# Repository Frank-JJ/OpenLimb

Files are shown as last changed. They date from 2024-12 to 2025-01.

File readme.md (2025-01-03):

# OpenLimb

This project contains code for the OpenLimb project at University of Southern Denmark, SDU, for the Fall 2024 semester.

This project consists of the design and construction of a bio-inspired robot, with limbs made of soft material, allowing for locomotion.

The code in this repository enables the functionality of the robot, when it is assembled correctly.

## Building the robot

### Components List

- **1 pcs.**   Raspberry Pi Pico W
- **1 pcs.** Android-compatible Bluetooth gamepad, e.g. 8BitDo Pro 2 Bluetooth Gamepad
- **4 pcs.**   MG90S Micro Servo Motor
- **1 pcs.**   Li-ion-PO 7.4V 1000mAh battery
- **1 m.**      Fishing line
- **4 pcs.**   5V Linear Voltage Regulator (L7805ACV)
- **10 pcs.**  Female-Female Jumper Cables
- **1 pcs.**   USB to Micro-USB cable
- **12 pcs.** M2×7mm bolts
- **4 pcs.**  M2×16mm bolts
- **16 pcs.** M2 nuts
- **16 pcs.** M2 washers

In addition to the components listed, it is highly recommended to acquire a fireproof battery bag, a balanced cell charger, and a over-, under-charge alarm for the battery. Handle the Li-ion battery with care!
The electrical circuit may require more or less jumper cables, and with different connectors.

### Manufacturing and 3D printing

Any modern 3D printer should be able to print the parts required for this project. You will need either PLA or PETG for:

- Base
- Battery Mount
- Feet
- Mounting clip
- Pulley
- Servo mount

Besides that, the legs need to be printed in PETG to be flexible and the fins need to be printed in TPU for bendability and grippyness.

### Assembly of Robot

Now that all the parts has been manufactured, it is time to assemble the robot. The robot can be assembled in different configurations to meet a specific task at hand. This configuration can be changed later if necessary.

#### Assembly of Limbs

One limb is constructed using the following parts:

- **1 pcs.**   Flexible 3D-printed or laser cut sheet
- **1 pcs.**   3D-printed magnet/motor mount
- **1 pcs.**   MG90S Micro Servo motor
- **1 pcs.**   Friction pad
- **2 pcs.**   Neodymium Magnets
- **1 pcs.**   3D-printed foot
- **$\approx 30cm$**   Fishing line
- **1 pcs.**   Pulley

Assemble the limb by following these steps:

- STEPS

#### Connecting Limbs to the Body

The limbs can be attached in many configurations around the robot's body. Determine a suitable position for the limb, and then dis-attach the ring cover from the underside of the robot's body with a twisting motion counter-clockwise. Carefully place two Neodymium Magnets in the indents at the chosen position in the robot body. Secure the ring cover over the magnets, by twisting it clockwise until it's locked in place.

Turn the robot around, and place the 3D-printed magnet/motor mount at the end of the limb above the magnets in the body. When the limb has snapped in place, insert a pin into the hole in the magnet/motor mount to lock it in place.

Repeat for the amount of limbs in the desired configuration.

#### Electrical Assembly

- **1 pcs.**   Raspberry Pi Pico W
- **1 pcs.**   Li-ion-PO 7.4V 1000mAh battery
- **4 pcs.**   5V Linear Voltage Regulator (L7805ACV)
- **10 pcs.**  M Jumper Cables
- **4 pcs.**   M3x15 Machine Screws

Secure the Raspberry Pi Pico W with four M3x15 machine screws in the middle of the robot body. Solder or use quick connect screw terminal blocks to replicate the schematic in [Electrical Schematic](#electrical-diagram):

#### Electrical Diagram

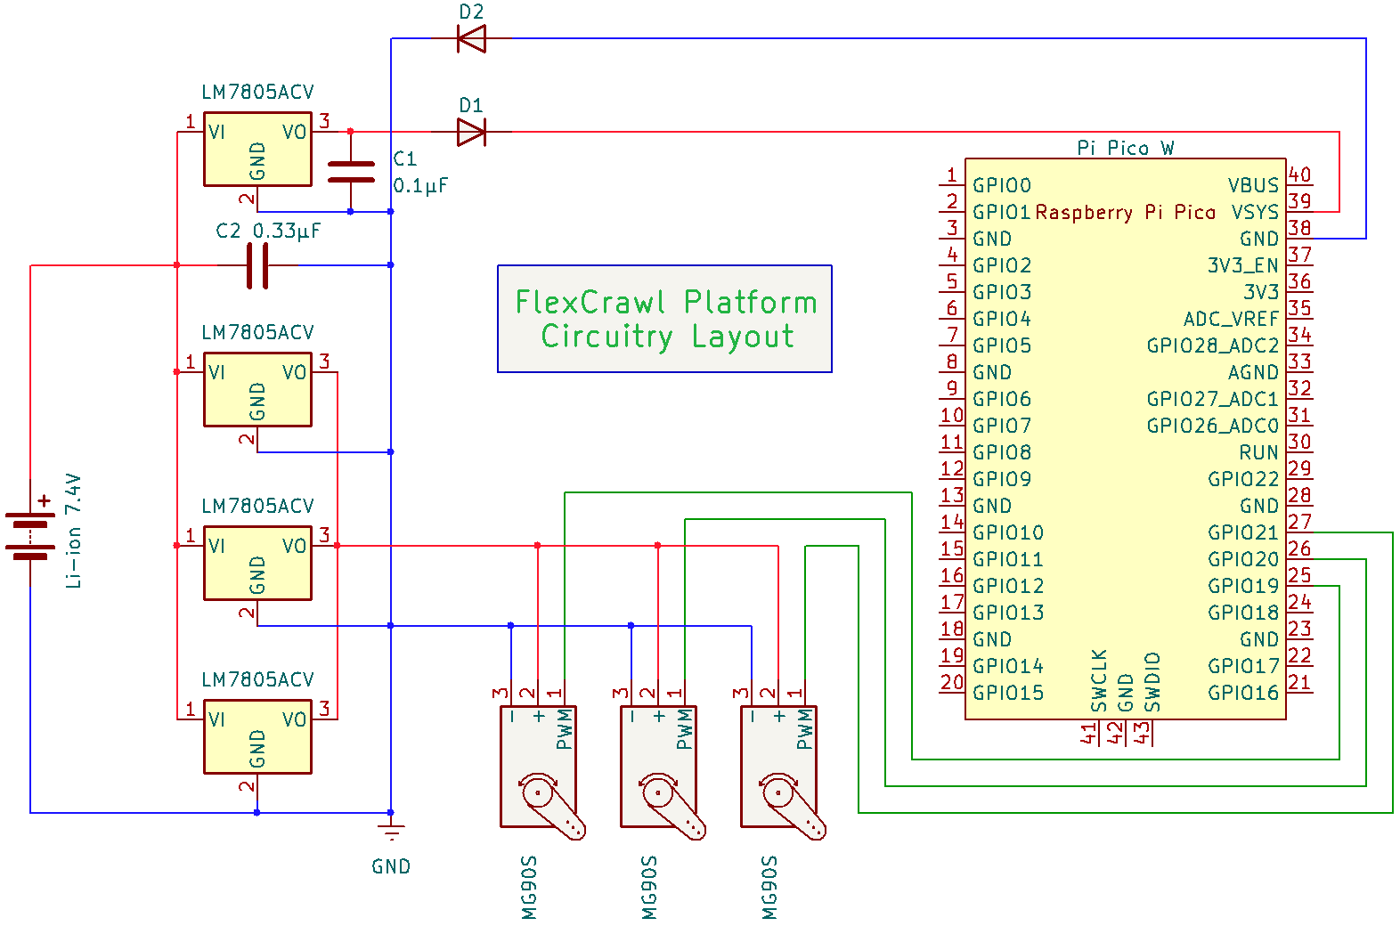
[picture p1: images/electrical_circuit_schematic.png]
Schematic showing the different components and their connections


Use electrical tape to fasten components to the body if necessary, but keep in mind to keep weight as low as possible.

## Using the code

The "flexControl" arduino project contains code that should be run on the Raspberry Pi Pico W to control the servos, according to user defined gaits.

The code consists of three parts:

- A bluetooth handler, for obtaining user input from a bluetooth compatible joystick.
- The gait machine, which linearly interpolates between defined motor commands, to run a gait.
- The motor controller, which outputs the interpolated values from the gait machine to the servos on the limbs.

### Configuring the three motors and limbs

The limb and motor configuration, when limited to three each, can be updated simply in [flexControl/gaitMachine.cpp](flexControl/gaitMachine.cpp):

Set the motor configurations in the MotorConfigVector variable. A limb can be placed on either the left, center, or right side of the body.
A servo can be placed on either the left or right side of the servo mount as seen from the body out along the length of the limb.

```cpp
line 180:   MotorConfigVector motorConfigVector = {
line 181:     {BodySide::Left, ServoSide::Left},
line 182:     {BodySide::Center, ServoSide::Left},
line 183:     {BodySide::Right, ServoSide::Left}
line 184:   };
```

The index defines the limb and motor. These indexes are further defined in [flexControl/gaitMachine.h](flexControl/gaitMachine.h):

Define the motor id's. These define the order of the motors in regards to what limbs they are attached to.

```cpp
line 15:    enum Motors {Right=0, Tail=1, Left=2};
```

### Defining a gait

#### Example gait

A gait can be defined as follows:

```cpp
GaitStruct Caterpillar = {
  .initialMotorPositions = {0,0,0},
  .gait={
    {Tail,  0.68,  0,    0.2},
    {Left,  0.9,  0,    0.5},
    {Right, 0.9,  0,    0.5},
    {Tail,  0.2,  0.5,  0.2},
    {Left,  0,    0.8,  0.05},
    {Right, 0,    0.8,  0.05},
    {Tail,  0,    0.8,  0.2},
  },
  .gait_time=0.5,
  .gait_amp=0.5
};
```

It must then be inserted into the movementGaits variable in [flexControl/gaitMachine.cpp](flexControl/gaitMachine.cpp):

```cpp
line 177:   GaitVector movementGaits = {Crawler, Caterpillar, TailPush, BackJump};
```

It can then be selected by the arrow or X, B, Y, A buttons of the joystick, by selecting the currect button according to its index in the vector.

#### The code structure

A gait is a vector of motor commands, as well as amplitude and duration parameters and initial motor positions.

The GaitStruct type in [flexControl/gaitMachine.h](flexControl/gaitMachine.h) defines the gait:

```cpp
line 30:    struct GaitStruct{
line 31:      std::vector<float> initialMotorPositions = {0,0,0};
line 32:      Gait gait;
line 33:      float gait_time = 2;
line 34:      float gait_amp = 1;
line 35     };
```

The gait_time parameter is the duration of the gait in seconds. The gait_amp parameter is the amplitude of the gait as a percentage of the max motor value, which is given in degrees:

```cpp
line 90:    float MOTOR_MAX_VAL = 180;
```

The gait parameter is a vector of motorCMD:

```cpp
line 26:    typedef std::vector<motorCMD> Gait;
```

A motorCMD consists of a motor id, amount of gait amplitude in percentage, start time and duration as a percentage of gait duration:

```cpp
line 18:    struct motorCMD{
line 19:      Motors motorID;
line 20:      float amount;
line 21:      float start;
line 22:      float duration;
line 23:    };
```

### Changing the number of motors and limbs

The default code allows for three servos, but this can be modified.

#### Within the motor controller

Go into: [flexControl/motorControl.h](flexControl/motorControl.h)

Define the number of servos:

```cpp
line 36:    void loop(std::array<uint8_t, 3> servoVals);
line 39:    static const int NUM_SERVOS = 3;
```

Define the pins for each servo.

```cpp
line 42:    uint8_t servoPins[NUM_SERVOS] = {19,20,21};
```

Pinout for the Raspberry Pi Pico W Follow the pinout for the Raspberry Pi Pico W.

Define the min and max pulse width in microseconds for the min and max angle of each servo (<https://docs.arduino.cc/libraries/servo/>):

```cpp
line 43:    uint16_t servoMins[NUM_SERVOS] = {544,544,544};
line 44:    uint16_t servoMaxs[NUM_SERVOS] = {2400,2400,2400};
```

#### Within the gait machine

##### Within the h file

Go into: [flexControl/gaitMachine.h](flexControl/gaitMachine.h)

Define the motor id's. These define the order of the motors in regards to what limbs they are attached to.

```cpp
line 15:    enum Motors {Right=0, Tail=1, Left=2};
```

Update the output from the loop function. The 3 should be changed to the number of motors:

```cpp
line 74:    std::array<uint8_t, 3> loop(bluetoothHandler::BluetoothOutput btIn);
```

Do the same for each of the arrays used to store motor values:

```cpp
line 83:    std::array<uint8_t, 3> program_end_motorpos = {0,0,0};
line 84:    std::array<float, 3> prev_M_pos = {0,0,0};
line 85:    std::array<float, 3> M_pos = {0,0,0};
line 87:    std::vector<float> MOTOR_INIT = {0,0,0};
line 98:    std::array<uint8_t, 3> motor_pos_array;
```

##### Within the cpp file

Go into: [flexControl/gaitMachine.cpp](flexControl/gaitMachine.cpp)

Set the motor configurations in the MotorConfigVector variable. A limb can be placed on either the left, center, or right side of the body.
A servo can be placed on either the left or right side of the servo mount as seen from the body out along the length of the limb.

```cpp
line 180:   MotorConfigVector motorConfigVector = {
line 181:     {BodySide::Left, ServoSide::Left},
line 182:     {BodySide::Center, ServoSide::Left},
line 183:     {BodySide::Right, ServoSide::Left}
line 184:   };
```

Add another mapping value to store the interpolated motor value:

```cpp
line 203:   static int M1_mapped = 0, M2_mapped = 0, M3_mapped = 0;
```

Expand the temporary motor position variables:

```cpp
line 217:   // Store initial motor values
line 218:   prev_M_pos[0] = MOTOR_INIT[0];
line 219:   prev_M_pos[1] = MOTOR_INIT[1];
line 220:   prev_M_pos[2] = MOTOR_INIT[2];
line 221:   M_pos[0] = MOTOR_INIT[0];
line 222:   M_pos[1] = MOTOR_INIT[1];
line 223:   M_pos[2] = MOTOR_INIT[2];
```

Expand the mapping and outputtin of motor values:

```cpp
line 266:   // Finally map the modified interpolated motor commands to the currect motor max and min values
line 267:   M1_mapped = mapToMotorValue(M_pos[0]);
line 268:   M2_mapped = mapToMotorValue(M_pos[1]);
line 269:   M3_mapped = mapToMotorValue(M_pos[2]);
line 270:   motor_pos_array = {(uint8_t)M1_mapped, (uint8_t)M2_mapped, (uint8_t)M3_mapped};
```

Expand the initial motor positions output (the {0,0,0}) from the selectGait function:

```cpp
line 303:   return {{0,0,0}, movementGaits[0].gait, 0, 0, 0.5, 0};
```

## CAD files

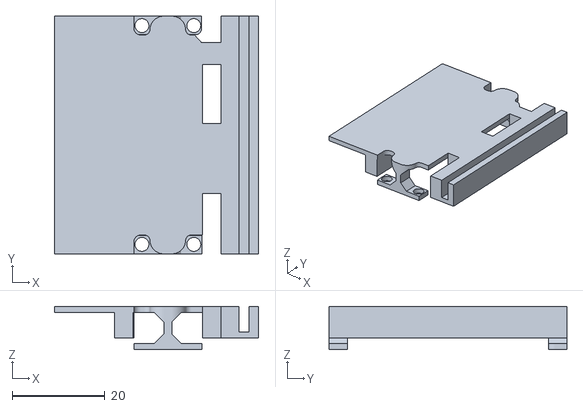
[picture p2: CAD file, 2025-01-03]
3D_Files/BatteryMount.stl
44.1 x 51.4 x 9.40

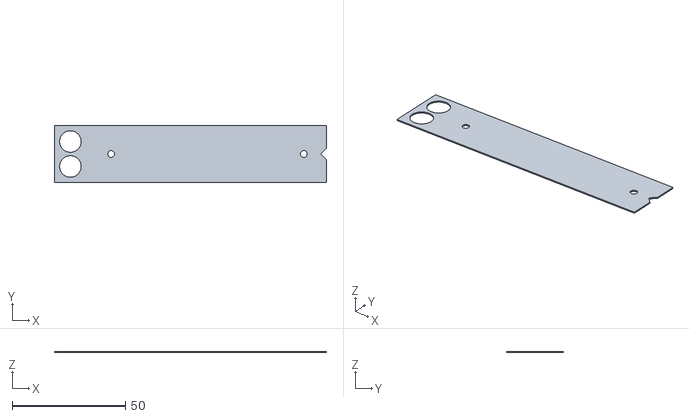
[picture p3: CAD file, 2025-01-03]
3D_Files/Legs/05.stl
120.0 x 25.0 x 0.5

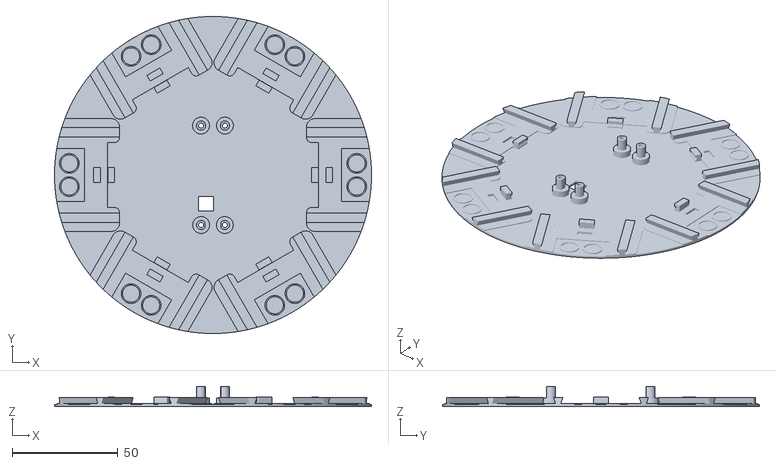
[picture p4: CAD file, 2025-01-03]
3D_Files/Base.stl
150.0 x 150.0 x 9.50

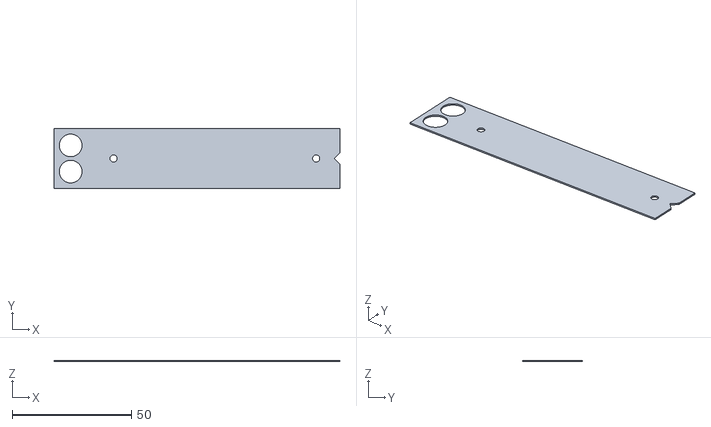
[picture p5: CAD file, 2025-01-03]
3D_Files/Legs/06.stl
120.0 x 25.0 x 0.6

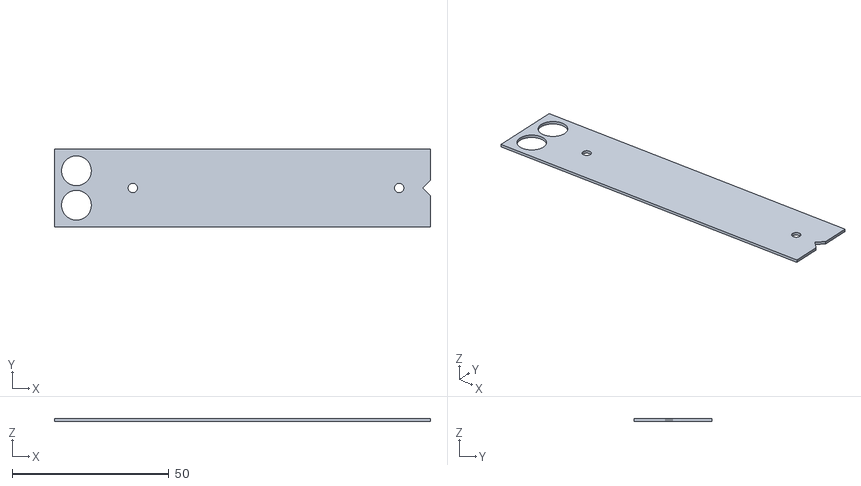
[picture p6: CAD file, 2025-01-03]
3D_Files/Legs/09.stl
120.0 x 25.0 x 0.9

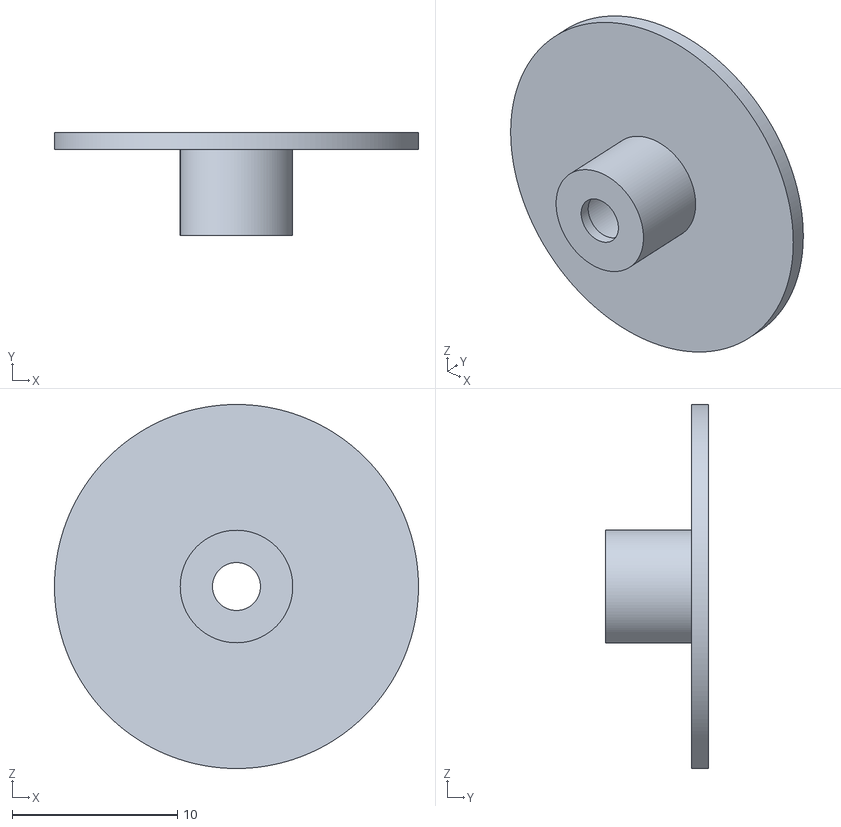
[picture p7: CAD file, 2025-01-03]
3D_Files/Pulley_lid.stl
22.0 x 6.20 x 22.0

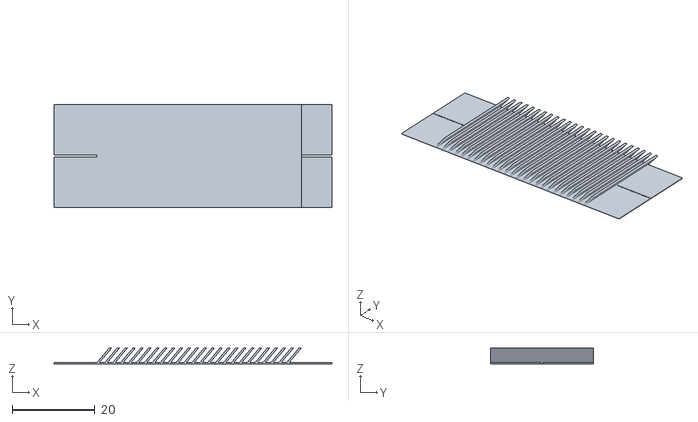
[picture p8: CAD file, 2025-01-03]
3D_Files/Fin.stl
67.4 x 25.0 x 3.82

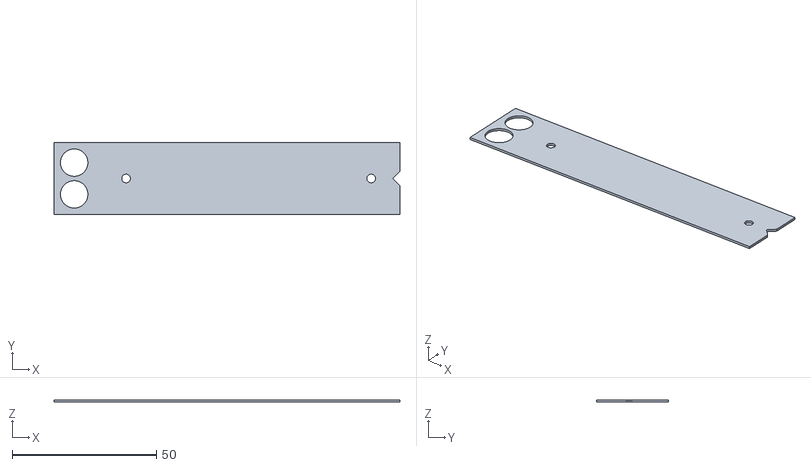
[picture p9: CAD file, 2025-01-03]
3D_Files/Legs/08.stl
120.0 x 25.0 x 0.8

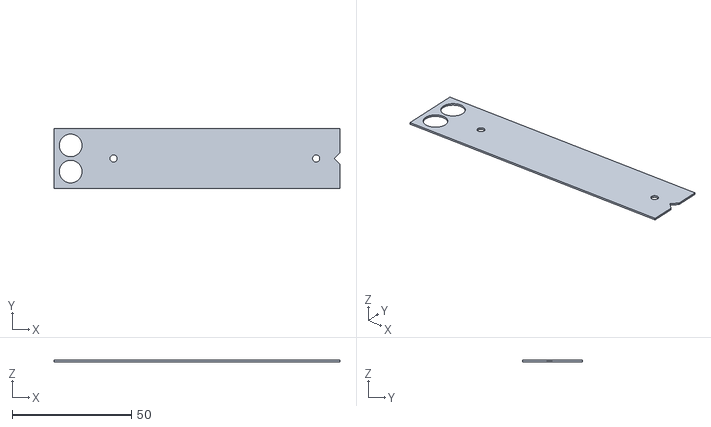
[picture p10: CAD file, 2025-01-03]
3D_Files/Legs/07.stl
120.0 x 25.0 x 0.7

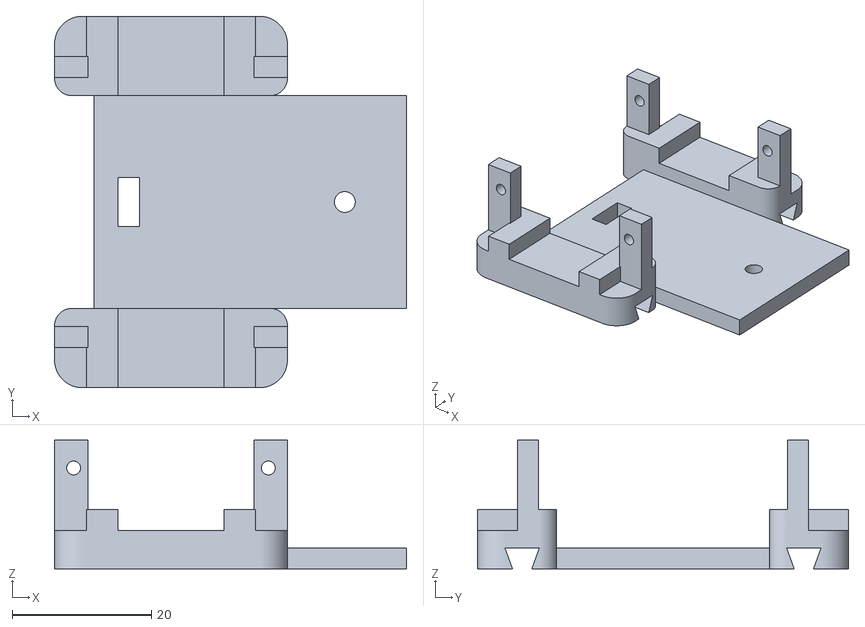
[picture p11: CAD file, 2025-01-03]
3D_Files/ServoMount.stl
50.6 x 53.4 x 18.5

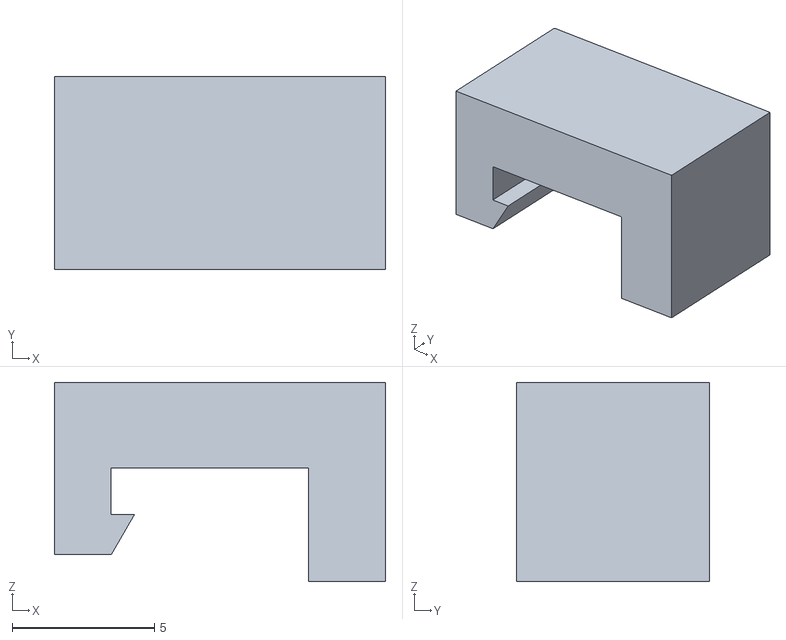
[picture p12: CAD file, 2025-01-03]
3D_Files/Mount_Clip.stl
11.6 x 6.80 x 7.00

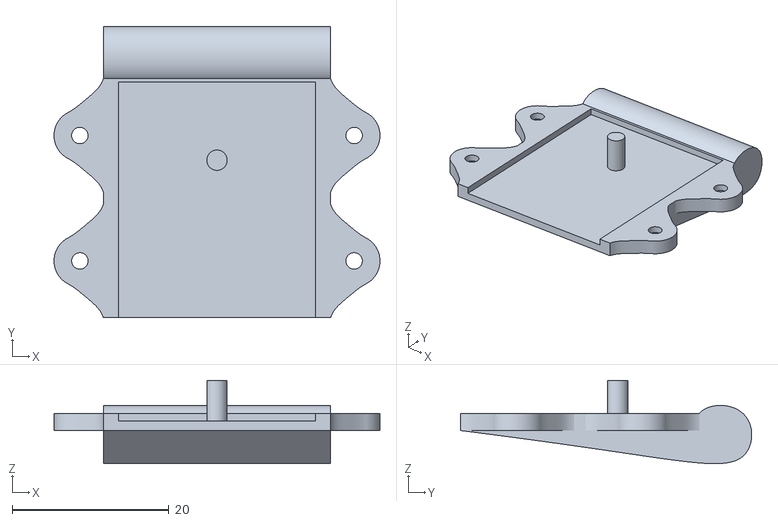
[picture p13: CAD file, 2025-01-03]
3D_Files/Feet_Bottom.stl
41.6 x 37.2 x 10.6

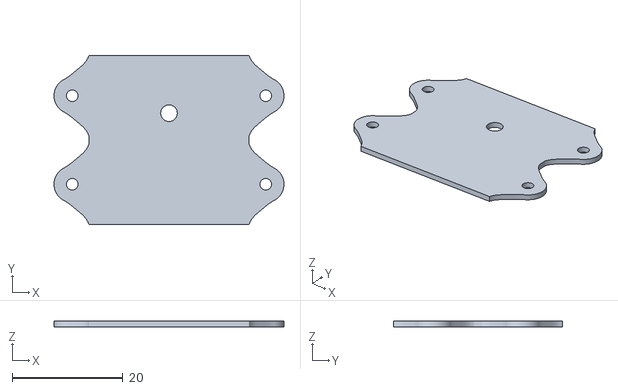
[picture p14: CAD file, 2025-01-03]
3D_Files/Feet_Top.stl
41.6 x 30.5 x 1.00

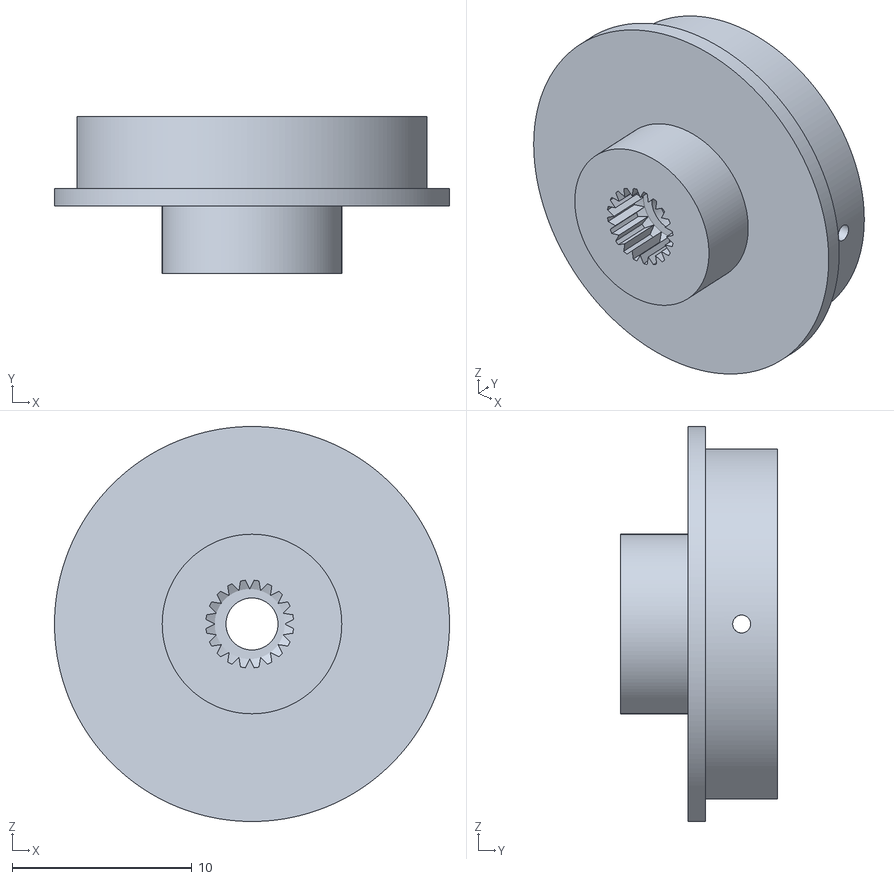
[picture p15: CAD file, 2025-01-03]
3D_Files/Pulley.stl
22.0 x 8.75 x 22.0

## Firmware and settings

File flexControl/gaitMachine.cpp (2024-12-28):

#include "SerialUSB.h"
#include "gaitMachine.h"

using namespace gaits;
using namespace bluetoothHandler;

GaitStruct MAX_MOTOR = {
  .initialMotorPositions = {1,1,1},
  .gait={
    {Motors::Tail, 1, 0, 1},
    {Motors::Left, 1, 0, 1},
    {Motors::Right, 1, 0, 1}
  },
  .gait_time=5,
  .gait_amp=1
};


GaitStruct MIN_MOTOR = {
  .gait={
    {Motors::Tail, 0, 0, 1},
    {Motors::Left, 0, 0, 1},
    {Motors::Right, 0, 0, 1}
  },
  .gait_time=5,
  .gait_amp=1
};

GaitStruct Crawler_50 = {
  .gait={
      {Motors::Tail, 0.8, 0, 0.1},
      {Motors::Left, 0.8, 0.1, 0.35},
      {Motors::Tail, 0, 0.1, 0.35},
      {Motors::Left, 0, 0.45, 0.05},
      {Motors::Tail, 0.8, 0.5, 0.1},
      {Motors::Right, 0.8, 0.6, 0.35},
      {Motors::Tail, 0, 0.6, 0.35},
      {Motors::Right, 0, 0.95, 0.05}
  },
  .gait_time=4,
  .gait_amp=1
};

GaitStruct Crawler_100 = {
  .gait={
      {Motors::Tail, 0.8, 0, 0.1},
      {Motors::Left, 0.8, 0.1, 0.35},
      {Motors::Tail, 0, 0.1, 0.35},
      {Motors::Left, 0, 0.45, 0.05},
      {Motors::Tail, 0.8, 0.5, 0.1},
      {Motors::Right, 0.8, 0.6, 0.35},
      {Motors::Tail, 0, 0.6, 0.35},
      {Motors::Right, 0, 0.95, 0.05}
  },
  .gait_time=2,
  .gait_amp=1
};

GaitStruct Crawler_200 = {
  .gait={
      {Motors::Tail, 0.8, 0, 0.1},
      {Motors::Left, 0.8, 0.1, 0.35},
      {Motors::Tail, 0, 0.1, 0.35},
      {Motors::Left, 0, 0.45, 0.05},
      {Motors::Tail, 0.8, 0.5, 0.1},
      {Motors::Right, 0.8, 0.6, 0.35},
      {Motors::Tail, 0, 0.6, 0.35},
      {Motors::Right, 0, 0.95, 0.05}
  },
  .gait_time=1,
  .gait_amp=1
};

GaitStruct TailPush = {
  .gait={
      {Motors::Tail, 0.8, 0, 0.1},
      {Motors::Tail, 0, 0.1, 0.35},
      {Motors::Tail, 0.8, 0.5, 0.1},
      {Motors::Tail, 0, 0.6, 0.35}
  },
  .gait_time=2,
  .gait_amp=1
};

GaitStruct Worm = {
  .gait={
    {Motors::Tail,  0.68,  0,    0.2},
    {Motors::Left,  0.9,  0,    0.5},
    {Motors::Right, 0.9,  0,    0.5},
    {Motors::Tail,  0.2,  0.5,  0.2},
    {Motors::Left,  0,    0.8,  0.05},
    {Motors::Right, 0,    0.8,  0.05},
    {Motors::Tail,  0,    0.8,  0.2}
  },
  .gait_time=1,
  .gait_amp=1
};

GaitStruct Jump = {
  .gait={
    {Motors::Tail, 1.0, 0, 0.001},
    {Motors::Tail, 0.0, 0.4, 0.1}
  },
  .gait_time=2,
  .gait_amp=0.5
};

GaitStruct WormR = {
  .gait={
    {Motors::Tail,  0.68,  0,    0.2},
    {Motors::Left,  0.5,  0,    0.5},
    {Motors::Right, 0.9,  0,    0.5},
    {Motors::Tail,  0.2,  0.5,  0.2},
    {Motors::Left,  0,    0.8,  0.05},
    {Motors::Right, 0,    0.8,  0.05},
    {Motors::Tail,  0,    0.8,  0.2}
  },
  .gait_time=2,
  .gait_amp=0.5
};

GaitStruct PushLegs = {
  .gait={
    {Motors::Left,  1,  0,    0.5},
    {Motors::Right, 1,  0,    0.5},
    {Motors::Left,  0,  0.5,  1},
    {Motors::Right, 0,  0.5,  1},
  },
  .gait_time=5,
  .gait_amp=1
};

GaitStruct PushTail = {
  .gait={
    {Motors::Tail,  1,  0,    0.5},
    {Motors::Tail,  0,  0.5,  1},
  },
  .gait_time=5,
  .gait_amp=1
};

GaitStruct UP_DOWN3 = {
  .initialMotorPositions = {0,0,0},
  .gait={
    {Motors::Tail, 0.8, 0, 0.8},
    {Motors::Tail, 0, 0.8, 1}
  },
  .gait_time=1,
  .gait_amp=1
};
GaitStruct UP_DOWN2 = {
  .initialMotorPositions = {0,0,0},
  .gait={
    {Motors::Right, 0.8, 0, 0.8},
    {Motors::Right, 0, 0.8, 1}
  },
  .gait_time=1,
  .gait_amp=1
};
GaitStruct UP_DOWN1 = {
  .initialMotorPositions = {0,0,0},
  .gait={
    {Motors::Left, 0.8, 0, 0.8},
    {Motors::Left, 0, 0.8, 1}
  },
  .gait_time=1,
  .gait_amp=1
};
GaitStruct BackJump = {
  .initialMotorPositions = {0,0,0},
  .gait={
    {Motors::Left, 1, 0, 0.5},
    {Motors::Right, 1, 0, 0.5},
    {Motors::Left, 0, 0.5, 0.5},
    {Motors::Right, 0, 0.5, 0.5}
  },
  .gait_time=0.5,
  .gait_amp=1
};
GaitStruct BackCrawl = {
  .gait={
      {Motors::Left, 1, 0, 0.25},
      {Motors::Left, 0, 0.25, 0.25},
      {Motors::Right, 1, 0.5, 0.25},
      {Motors::Right, 0, 0.75, 0.25}
  },
  .gait_time=1,
  .gait_amp=1
};
GaitStruct Caterpillar_50 = {
  .gait={
      {Tail,  0.68,  0,    0.2},
      {Left,  0.9,  0,    0.5},
      {Right, 0.9,  0,    0.5},
      {Tail,  0.2,  0.5,  0.2},
      {Left,  0,    0.8,  0.05},
      {Right, 0,    0.8,  0.05},
      {Tail,  0,    0.8,  0.2},
  },
  .gait_time=2,
  .gait_amp=0.5
};
GaitStruct Caterpillar_100 = {
  .gait={
      {Tail,  0.68,  0,    0.2},
      {Left,  0.9,  0,    0.5},
      {Right, 0.9,  0,    0.5},
      {Tail,  0.2,  0.5,  0.2},
      {Left,  0,    0.8,  0.05},
      {Right, 0,    0.8,  0.05},
      {Tail,  0,    0.8,  0.2},
  },
  .gait_time=1,
  .gait_amp=0.5
};
GaitStruct Caterpillar_200 = {
  .gait={
      {Tail,  0.68,  0,    0.2},
      {Left,  0.9,  0,    0.5},
      {Right, 0.9,  0,    0.5},
      {Tail,  0.2,  0.5,  0.2},
      {Left,  0,    0.8,  0.2},
      {Right, 0,    0.8,  0.2},
      {Tail,  0,    0.8,  0.2},
  },
  .gait_time=0.5,
  .gait_amp=0.5
};

GaitStruct Caterpillar_test_1 = {
  .gait={
      {Tail,  0.8,  0,    0.1},
      //{Left,  0.8,    0.1,   0.5},
      //{Right, 0.8,    0.1,   0.5},
      //{Tail,  0,    0.6,  0.4},
      //{Left,  0,    0.8,  0.2},
      //{Right, 0,    0.8,  0.2},
  },
  .gait_time=2,
  .gait_amp=1
};

GaitStruct Caterpillar_test_2 = {
  .gait={
      {Tail,  0.8,  0,    0.1},
      {Left,  0.8,    0.1,   0.5},
      {Right, 0.8,    0.1,   0.5},
      //{Tail,  0,    0.6,  0.4},
      //{Left,  0,    0.8,  0.2},
      //{Right, 0,    0.8,  0.2},
  },
  .gait_time=2,
  .gait_amp=1
};

GaitStruct Caterpillar_test_3 = {
  .gait={
      {Tail,  0.8,  0,    0.1},
      //{Left,  0.8,    0.1,   0.5},
      //{Right, 0.8,    0.1,   0.5},
      {Tail,  0,    0.6,  0.4},
      //{Left,  0,    0.8,  0.2},
      //{Right, 0,    0.8,  0.2},
  },
  .gait_time=2,
  .gait_amp=1
};

// Here we define the list of four gaits the joystick can change between
// We change between them with the arrow buttons, or X, B, Y, A buttons
// In order they are UP, DOWN, LEFT, RIGHT on the arrow buttons, or X, B, Y, A
GaitVector movementGaits = {Caterpillar_50, Caterpillar_100, Caterpillar_200, MIN_MOTOR};

// Here we define the motor and limb configurations
MotorConfigVector motorConfigVector = {
  {BodySide::Left, ServoSide::Left},
  {BodySide::Center, ServoSide::Left},
  {BodySide::Right, ServoSide::Left}
};

GaitMachine::GaitMachine()
{

}

GaitMachine::~GaitMachine()
{

}

// Here we map the interpolated motor values from the gait to actual servo values
int GaitMachine::mapToMotorValue(float M_pos){
  return (int)min(MOTOR_MAX_VAL,(M_pos * GAIT_AMP * MOTOR_MAX_VAL));
}
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

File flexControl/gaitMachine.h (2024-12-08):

#ifndef GAITMACHINE_H
#define GAITMACHINE_H

#pragma once

#include <vector>
#include <chrono>

#include <array>

#include "bluetoothHandler.h"

namespace gaits{
  // Defines order of limbs and thus what order their actuator values should be in when sent to motorControl
  enum Motors {Right=0, Tail=1, Left=2};

  // Defines a single movement command for a motor
  struct motorCMD{
    Motors motorID; // What motor id corresponding to one of the limbs defined in motors should be commanded
    float amount; // What percentage of the gait amplitude should it be commanded to
    float start; // When during a gait duration should the command start as a percentage
    float duration; // How long should the command take as a percentage of the gait duration
  };

  // The patter for a gait is a vector of motor commands
  typedef std::vector<motorCMD> Gait;

  // A gait has a duration and amplitude, as well as initial motor values.
  // These parameters are defined with a gait using this struct
  struct GaitStruct{
    std::vector<float> initialMotorPositions = {0,0,0}; // Here we define the initial motor values
    Gait gait; // Here the gait is inserted
    float gait_time = 2; // Duration of the gait's repeating pattern (seconds)
    float gait_amp = 1; // Amplitude of the gait. A percentage of MOTOR_MAX_VAL
  };

  // Gaits can be stored in a vector for easy indexin
  typedef std::vector<GaitStruct> GaitVector;

  // This struct defines the parameters used to define the currently running gait, based on additional parameters
  // These parameters are set based on either a defined GaitStruct or modified from joystick input
  struct GaitSelectionInfo{
    std::vector<float> motor_init = {0,0,0}; // These are the initial values as from GaitStruct
    Gait gait; // This is the gait pattern
    float gait_time = 2; // This is the gait time from a GaitStruct
    float gait_amp = 1; // This is the gait amplitude as from GaitStruct or from the joystick left stick FORWARDS/BACKWARDS
    float direction = 0; // This is the gait direction, a modifier to the left and right motors as defined by the MotorConfigVector. It is set by the joystick right stick LEFT/RIGHT. In the center both are activated at 100%, when turned all the way to the LEFT or RIGHT, the opposite side is set to 0%.
    float gait_time_modifier = 1; // This is a multiplier for the gait duration. This is set by joystick right stick FORWARDS/BACKWARDS. When the stick is FORWARDS the value becomes 0, and thus duration becomes zero. When BACKWARDS the value becomes 2, and duration is doubled.
  };

  // Each limb can be defined as being on the left, center, or right side of the robot body
  enum class BodySide {Left=0, Right=1, Center=2};

  // Each servo can be defined as being on the left or right side of the servo mount for a limb, when looking from the servo mount with the limb foot poiinting away from the viewer
  enum class ServoSide {Left=0, Right=1};

  // The limb and servo sides are encapsulated in a MotorConfig struct, and further in a vector of these
  struct MotorConfig{
    BodySide bodySide;
    ServoSide servoSide;
  };
  typedef std::vector<MotorConfig> MotorConfigVector;  
}

using namespace gaits;
using namespace std::chrono;

class GaitMachine
{
  public:
    GaitMachine();
    ~GaitMachine();
    void setup();
    std::array<uint8_t, 3> loop(bluetoothHandler::BluetoothOutput btIn);

  private:
    int mapToMotorValue(float M_pos);
    void gaitControl(Gait gait, std::chrono::microseconds deltaT = std::chrono::microseconds(0));
    GaitSelectionInfo selectGait(bluetoothHandler::BluetoothOutput btIn);
    
    std::array<int8_t, 3> running_commands = {-1,-1,-1};

    std::array<uint8_t, 3> program_end_motorpos = {0,0,0};
    std::array<float, 3> prev_M_pos = {0,0,0}; // When running a gait, we do linear interpolation in each motor command. For this we use the previous commands amount value stored in this variable. If there is no previous command we use the initial motor values
    std::array<float, 3> M_pos = {0,0,0};  // We store the current linearly interpolated motor values here

    std::vector<float> MOTOR_INIT = {0,0,0};
    float GAIT_T = 2;   // Duration of the gait's repeating pattern (seconds).
    float GAIT_AMP = 1;   // Max degree of amplitude.
    float MOTOR_MAX_VAL = 180; // Max degree of servos allowed.
    float MODE_DIR = 0; // Mode direction of gait. Goes from 0 to 1, where 0.5 is the center.
    float directionCenter = 0.5;
    float GAIT_T_AMP = 1; // Amplitude of gait duration. As in what to multiply GAIT_T with to get the final gait duration.
    
    float tick_frq = 200; // Hz
    microseconds tick_Time = duration_cast<microseconds>(std::chrono::duration<float>(1/tick_frq));

    std::array<uint8_t, 3> motor_pos_array;

    std::chrono::time_point<std::chrono::steady_clock> tick_start;
    std::chrono::time_point<std::chrono::steady_clock> last_call;

    
};

#endif

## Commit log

2024-09-24 Initial commit, with code for controlling the servos.
2024-10-09 Implementing bluetooth from the ground up, using arduino IDE, following https://github.com/usedbytes/picow_ds4/tree/main
2024-10-15 Basic implementation of pico w acting as hid master, and successfully connecting and recieving data from an android compatible wireless bluetooth controller.
2024-10-21 Finished initial solution for bluetooth joystick->gait->servo pipeline. Needs comments and cleanup!
2024-10-22 Changed motorControl to only send when new positions should be set. This makes gaitMachine control the frequency of servo control.
2024-10-22 Added gait time and motor max value to gait definitions, to allow customization. gait amplitude has been removed, since it is unneeded with motor max value existing.
2024-10-29 Reverted write and attach. Running attach first makes sure the servo goes to zero first.
    [motorControl.cpp]
2024-10-29 Bluetooth input code should be done, but it does not work...
    [bluetoothHandler.cpp, gaitMachine.cpp, gaitMachine.h]
2024-11-05 Fixing of bluetooth output in progress
    [bluetoothHandler.cpp, gaitMachine.cpp, gaitMachine.h]
2024-11-05 Implemented dynamic gait controlled with joystick. Motor 3 (index 2) seems to not move correctly.
    [bluetoothHandler.cpp, gaitMachine.cpp, gaitMachine.h]
2024-11-05 Fixed indexing problem with Motor 3 (index 2).
    [gaitMachine.cpp, gaitMachine.h]
2024-11-08 Reset previous motor position to zero.
    [gaitMachine.cpp, gaitMachine.h]
2024-11-12 Gait stops when arrow buttons are released now.
2024-11-12 Initial mode of gaits when using buttons instead of arrow-buttons is now the base mode of the gaits; the amplitude and duration is the same as in the gait definition, instead of being modified by 0.5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
2024-11-12 Fixed bug when changing to a gait that does not command all motors. They now correctly are reset to the initial motor position defined in the gait.
    [gaitMachine.cpp, gaitMachine.h]
2024-11-19 Cleaned up repo. Removed all except code used for the flexicrawl robot. (last commit was in error)
    [bluetoothHandler.cpp, gaitMachine.cpp, gaitMachine.h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]
2024-11-19 Added test code for testing motors with legs at different motor speeds.
2024-11-19 Added movement turn off on right bottom button, turn on by pressin on of the other four top right buttons.
2024-11-19 Arrow buttons left and right now change between gaits, each gait controls one motor.
2024-12-06 Tested gaits [Crawler, TailPush, BackJump, BackCrawl]. BackCrawl did not work, others worked suffeciently on wood surface, with defined gait values of BackJump, and default dynamic joystick values fo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
    [gaitMachine.cpp]
2024-12-08 Added readme to explain gait definition, limb and motor configuration, and changing the number of motors and limbs.
2025-01-03 Added the 3D printable files
    [05.stl, 06.stl, 07.stl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]
2025-01-03 Added Building the robot section to readme, together with schematic of electrical circuit.
